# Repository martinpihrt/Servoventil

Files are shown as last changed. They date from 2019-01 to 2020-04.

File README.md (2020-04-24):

# Servoventil
Servoventil pro zalévací systém řízený procesorem ATTINY 1634 napájený z 5 AA baterií (celkem 6V). Zařízení je postavené z SMD součástek jako finální produkt za co nejméně peněz. Schéma zapojení obsahuje pouze nejnutněší součástky a procesor, který není zbytečně velký (rozměrově a programově). Deska obsahuje DIP spínač pro nastavení časů.  Programovací konektor ICSP 2x5 pinů, LED signalizující vybité baterie a chod zařízení, konektor pro připojení serva MG996R, startovací tlačítko, konektor pro sériovou linku (možnost komunikace s procesorem). Program pro procesor je napsán v prostředí Arduino IDE.  
Cena celého zařízení vychází bez serva na cca 225 Kč.

* Pohled na osazenou desku HW:1.0
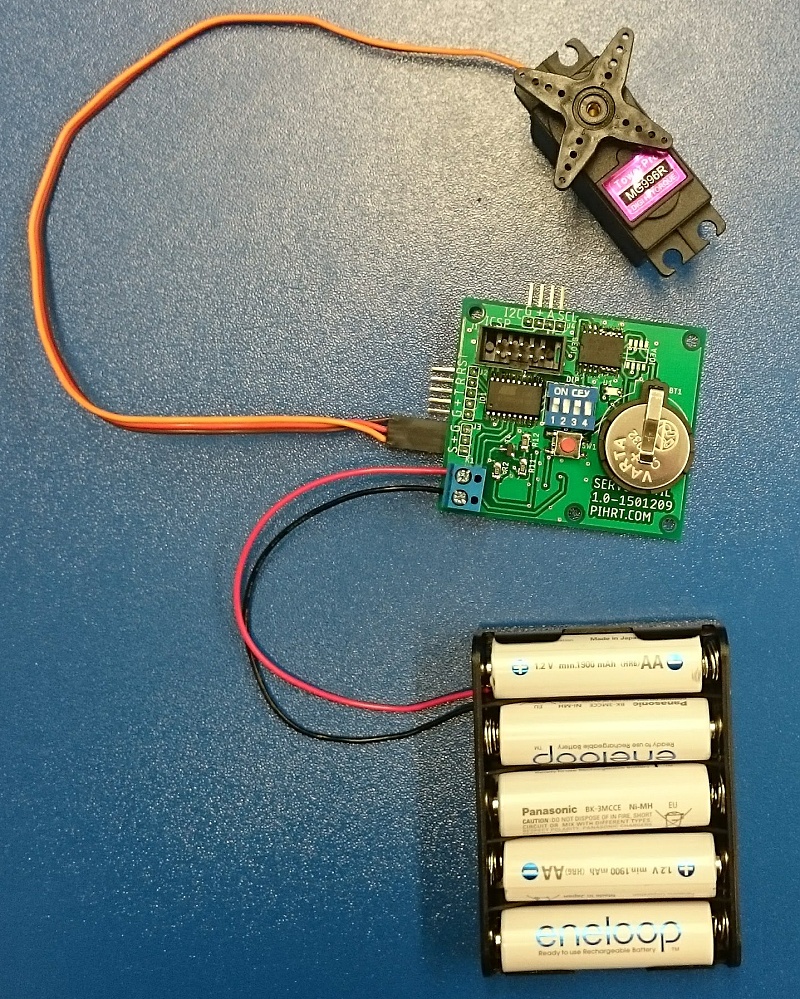
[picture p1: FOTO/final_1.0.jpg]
<br>
* Schéma zapojení HW:1.0
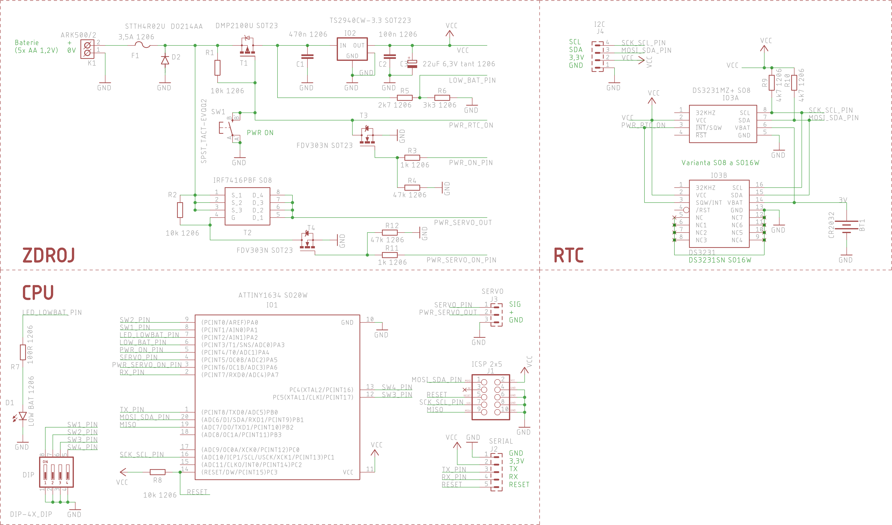
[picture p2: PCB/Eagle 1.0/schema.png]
<br>

# Funkce
## Uvedení do provozu
Po připojení napájení (5ks nabíjecí baterie AA 1,2V - celkem tedy 6-7V) čeká zařízení na stisk tlačítka. V tomto režimu neodebírá žádný proud z baterií (oba MOSFET tranzistory jsou udržovány uzavřené přes rezistory z kladného pólu). Časovač RTC ještě nebyl nastaven a má vloženu záložní baterii. Po stisknutí tlačítka na minimálně 1 sec se uzemní řídící vstup (gate) MOSFET tranzistoru, ten se otevře a přivede napájecí napětí na stabilizátor 3,3V. Za stabilizátorem je připojen procesor ATTINY 1634, který provede toto:
* sepne pomocný tranzistor, který podrží sepnutý (gate) u MOSFETu i po uvolnění tlačítka.
* změří napětí baterie (na AD vstupu procesoru je napětí z baterií 0-6V sníženo rezistorovým děličem na rozsah 0-3,3V). Napětí baterie se pohybuje (naprázdno) plně nabitého článku 1,4 V až napětí vybitého článku 1,0 V. Napětí pod 5V lze považovat za vybitý stav. Na AD vstupu naměříme hodnotu napětí (po zmenšení děličem) 2,6V. Pokud je baterie vybitá bliká LED dioda (3x blik, pauza, 3x blik...). RTC běží pouze z baterie a když je čas alarmu tak RTC přes svůj vnitřní tranzistor (otevřený kolektor) uzemní MOSFET, který sepne napájení pro stabilizátor a CPU. 
* přečte nastavené DIP spínače, sepne na určitý čas servo (napájení serva přes MOSFET a generuje signál pro odpovýdající směr a rychlost serva na určitou dobu) LED svítí -> ventil se otevře. Následně vypne napájení serva a čeká nastavenou dobu (dle DIP spínače 1-7 minut). Led bliká po dobu čekání otevření ventilu (krátké záblesky). Po nastavené době opět sepne napájení serva a ventil uzavře (LED svítí).
* nastaví čas (alarm) do RTC pro příští probuzení zařízení (cyklus 12, nebo 24 hodin).
* vypne veškeré napájení (běží pouze RTC z baterie).
* po nastavené době (DIP pozice 4: 12/24 hodin) RTC probudí CPU a opět se provede otevření ventilu na určitou dobu...

## DIP spínač má následující význam
Pozice 1-3 je BCD (dvojkový) kód pro nastvení doby otevření ventilu 1-7 minut.
* pozice 1 -> ON=1 minuta
* pozice 2 -> ON=2 minuty
* pozice 3 -> ON=4 minuty
Výsledný čas dle pozice 1-3 se sčítá. Příklad: čas otevření ventilu chceme 3 minuty -> DIP pozice 1 = ON, pozice 2 = ON, pozice 3 = OFF

Pozice 4 je čas probouzení.
* pozice 4 -> ON= 12 hodin, OFF= 24 hodin probouzení RTC časovače.

## Osazení desky spojů
Deska byla vyrobena u https://www.allpcb.com/.
* Pohled na desku TOP
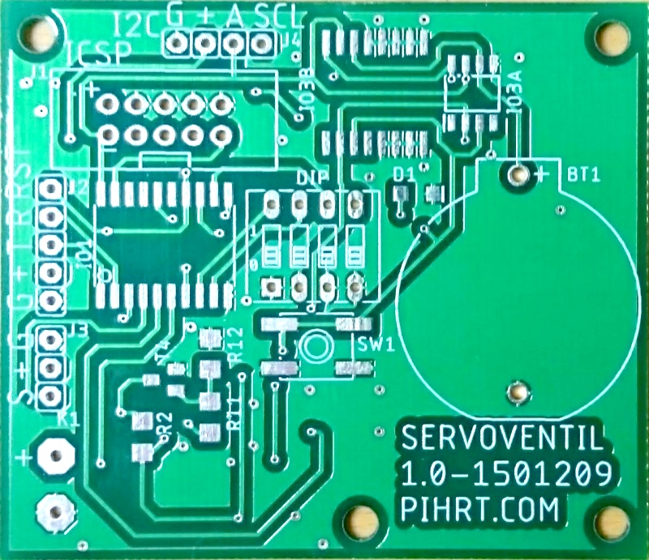
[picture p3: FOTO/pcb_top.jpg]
<br>
* Pohled na desku BOT
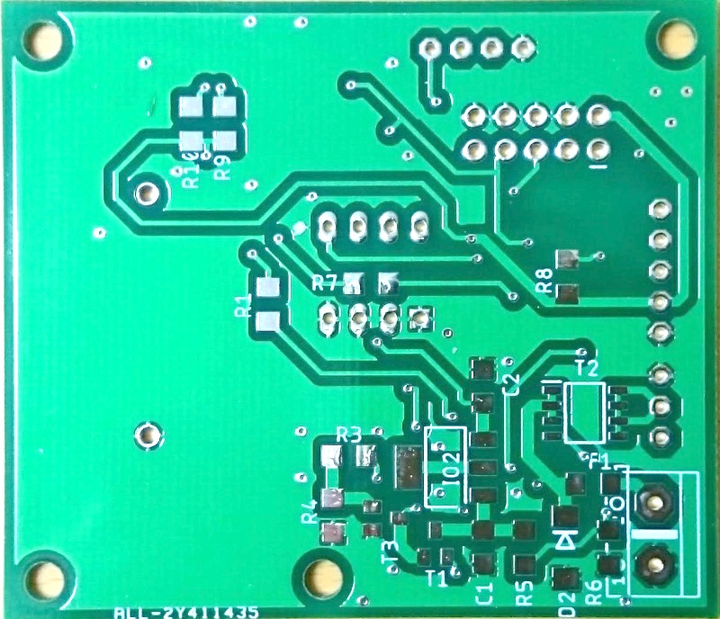
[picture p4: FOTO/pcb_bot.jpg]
<br>
První čím začneme je osazení SMD součástek z horní strany (TOP) a následně spodní (BOTTOM) strany. Po osazení SMD součástek zapájíme z horní strany THT (drátové) součástky - DIP spínače, držák baterie, napájecí konektor, řadové lišty. Před připojením napájení (baterie, nebo ICSP konektor) je potřeba desku pečlivě zkontrolovat na případné zkraty, nebo otočení součástek. Značení SMD rezistorů je následující: příklad text na rezistoru 1014 znamená 101 + 4 nuly tedy 101 0000 Ohmů, nebo 202 znamená 20 + 2 nuly tedy 20 00 Ohmů (2k).
Před připojením baterií (5ks AA) připojíme (pokud máme) napájecí zdroj s proudovou pojistkou, kterou nastavíme na 100 mA při 6V. Servo ani ICSP programátor není zatím k desce připojen. Obvod nemá v tuto chvíli ze zdroje odebírat žádný proud. Stiskneme a držíme tlačítko SW1 zmačknuté. Multimetrem (voltmetrem) změříme napětí na procesoru, RTC nebo stabilizátoru 3,3V. Napětí musí být cca 3,3V (při 6V na zdroji). Proud ze zdroje bude stále nepatrný (pár mA) - pouze se napájí procesor. Pokud se neobjevil problém (zkrat, velký podezřelý odběr proudu ze zdroje atd...) můžeme odpojit zdroj a zkusit připojit ICSP programátor. Nastavíme Arduino IDE na správný procesor a ICSP programátor. V tuto chvíli by již měl jít do procesoru nahrávat kód. Pokud připojíme na UART (sériovou linku) převodník, můžeme sledovat ladící výpisy co se aktuálně v procesoru odehrává. Protože je RTC obvod DS3231 jako samostatná součástka velmi drahý (okolo 200,-), tak ho odpájíme z China desky (ta se dá pořídit za 30,-).
* Pohled na osazenou desku TOP
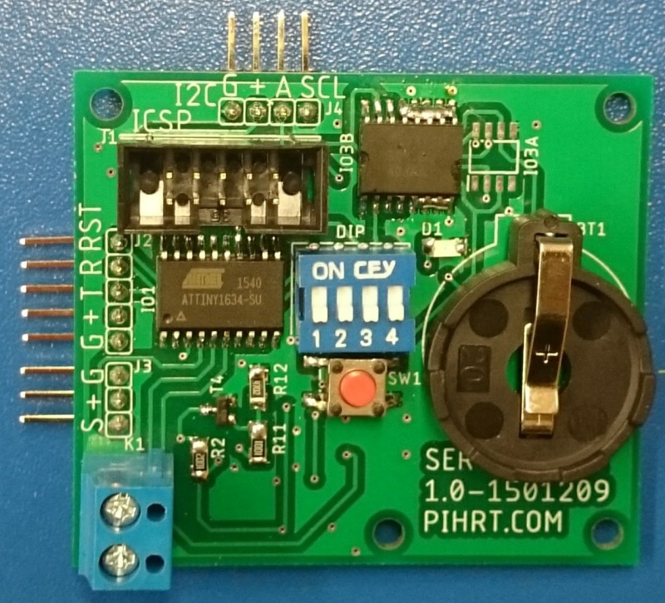
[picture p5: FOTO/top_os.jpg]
<br>
* Pohled na osazenou desku BOT
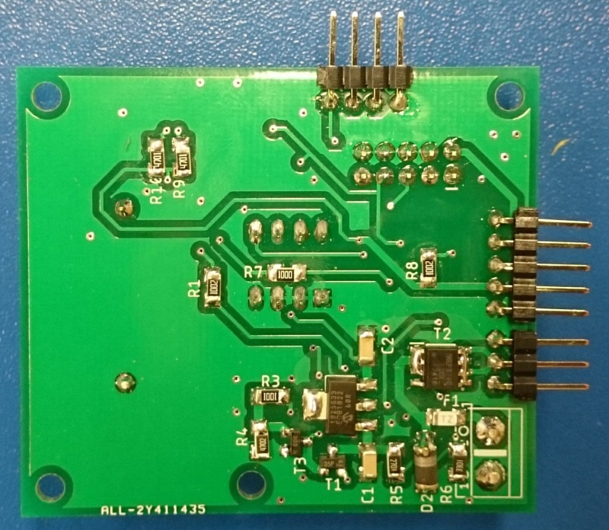
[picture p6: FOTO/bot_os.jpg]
<br>
* Připojení ICSP programátoru a USB-UART převodníku
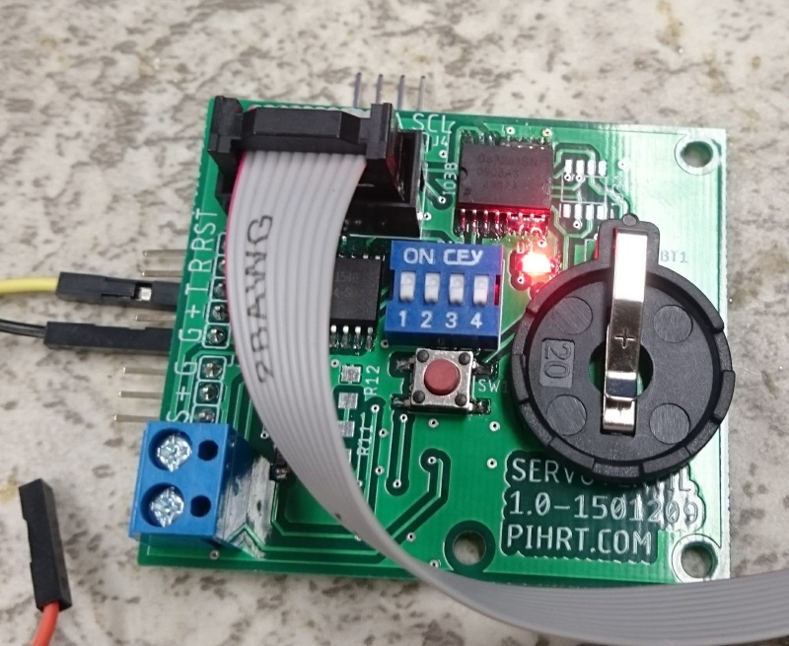
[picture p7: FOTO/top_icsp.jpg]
<br>
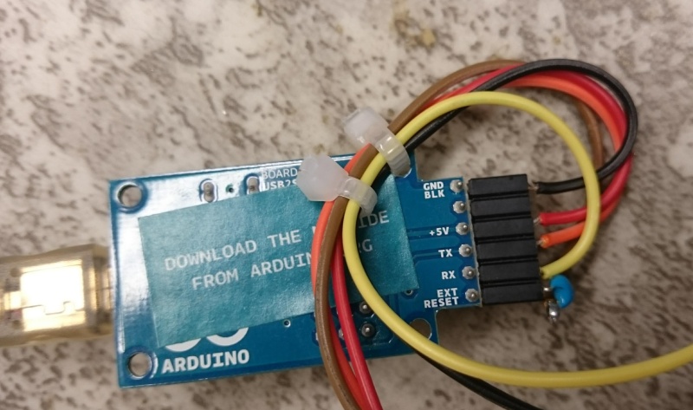
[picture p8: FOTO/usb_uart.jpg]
<br>
* Deska RTC s DS3231 (před vypájením a po vypájení)
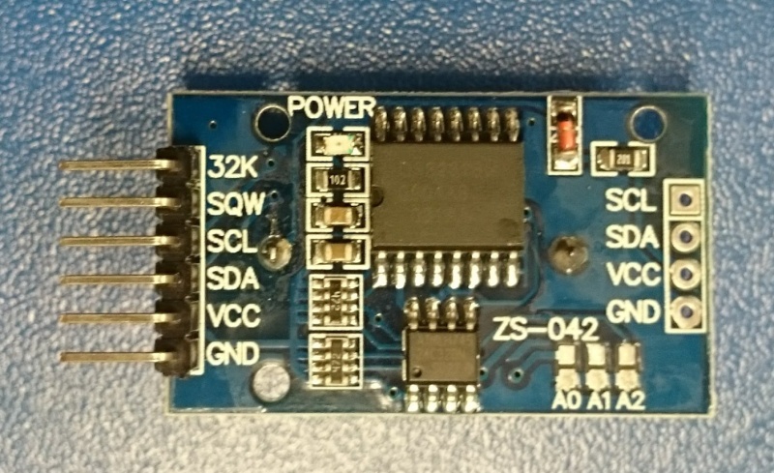
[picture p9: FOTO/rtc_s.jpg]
<br>
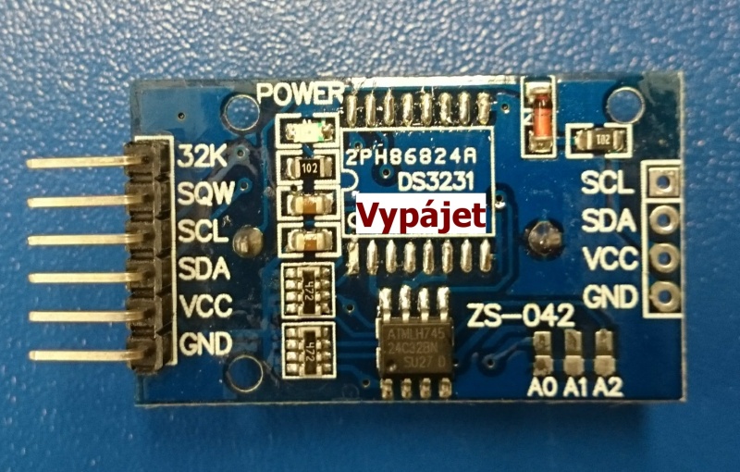
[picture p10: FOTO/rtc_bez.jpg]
<br>

## Přidání podpory pro procesor ATTINY 1634 do Arduino IDE
Spustíme nainstalované Arduino v našem počítači a otevřeme záložku "Soubor -> vlastnosti" a do správce dalších desek URL přidáme tento odkaz
http://drazzy.com/package_drazzy.com_index.json ze stránek [GitHub drazzy](https://github.com/SpenceKonde/ATTinyCore/blob/master/Installation.md). Následně potvrdíme tlačítkem "OK". Otevřeme v Arduinu záložku "Nástroje -> Vývojová deska -> Manažér desek" v otevřeném seznamu si vybereme "ATTinyCore by Spencle Konde" a přidáme do Arduina tlačítkem "instalace". V nastavení Arduino IDE je po těchto krocích možné využívat i jiné procesory než které jsou ve výchozí instalaci Arduina.

## Nahrání programu do desky - ICSP programátor
Připojíme do konektoru ICSP desky servoventilu náš programátor (pokud ho nemáme zakoupený, můžeme si ho vyrobit dle [tohoto návodu](https://pihrt.com/elektronika/390-programator-atmel-isp-usbasp)). Při připojení programátoru nepoužíváme napájení z baterií (baterie odpojíme)!

# Verze FW
* 1.0.0 výchozí verze programu 
* 0.0.0 výchozí verze programu - test všech periferií

# Verze HW
* 1.0 15.1.2019 výchozí verze desky 

# Licence
Creative Commons Attribution Share Alike 4.0
cc-by-sa-4.0

Na projektu se podílejí:
HW a FW Martin Pihrt - www.pihrt.com

# Aktuálně, TODO
## 23.4.2020
* Pracuji na verzi FW 1.0.0 (funkce dle popisu DIP a uvedení do provozu)

## 18.2.2019
* HW je otestován a plně funkční: pro test použit FW:0.0.0. Článek NiMh má 1,2 V. Napětí (naprázdno) plně nabitého článku je 1,4 V. Napětí vybitého článku je 1,0 V. Máme 5 článků -> napětí se bude pohybovat od 5V do 7V. Pod 5V je vybito LED blikne 2x krátce. Běží program - LED bliká rychle.

Výpis ze seriové linky (2 minuty probouzení)  
FW:0.0.0,18.2.2019,11:13:33  
RTC init...OK  
DIP1-4 init...OK  
DIP1=0 DIP2=1 DIP3=0 DIP4=1  
Baterie=5.86V  
Servo init...OK  
RTC nastavuji interval...OK  
Baterie=5.78V  
Baterie=5.85V  
Vypinam!

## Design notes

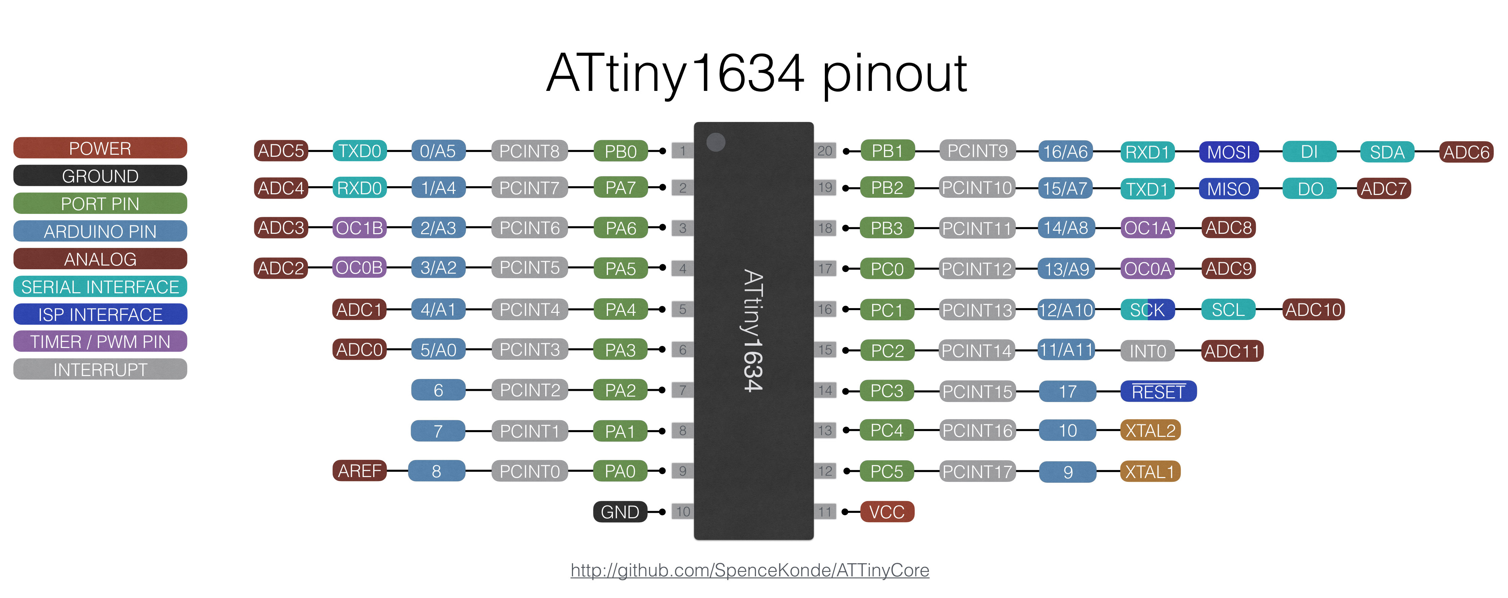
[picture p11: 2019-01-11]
FW/pinout attiny1634.jpg

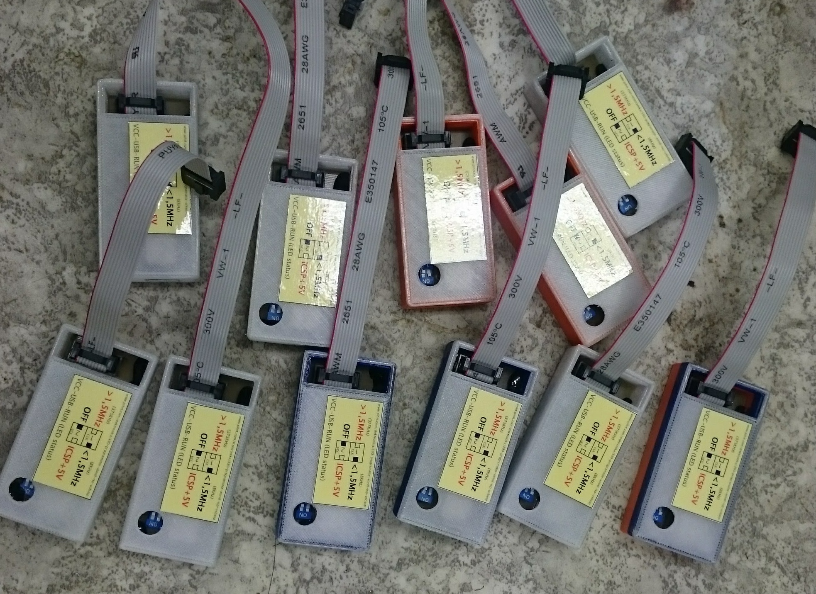
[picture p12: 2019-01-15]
FOTO/icsp_2.jpg

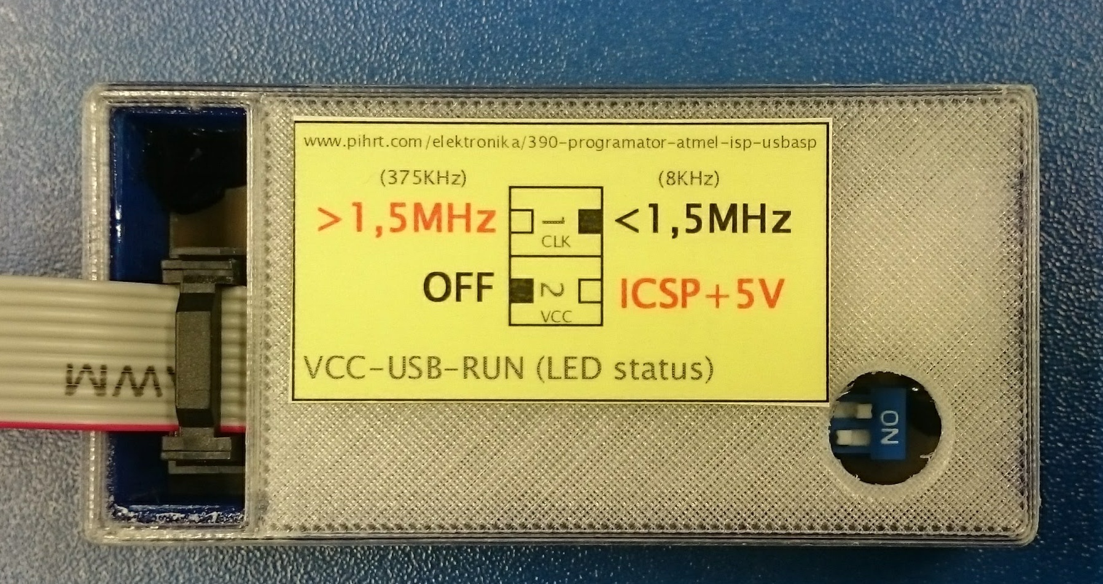
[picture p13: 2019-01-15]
FOTO/icsp_1.jpg

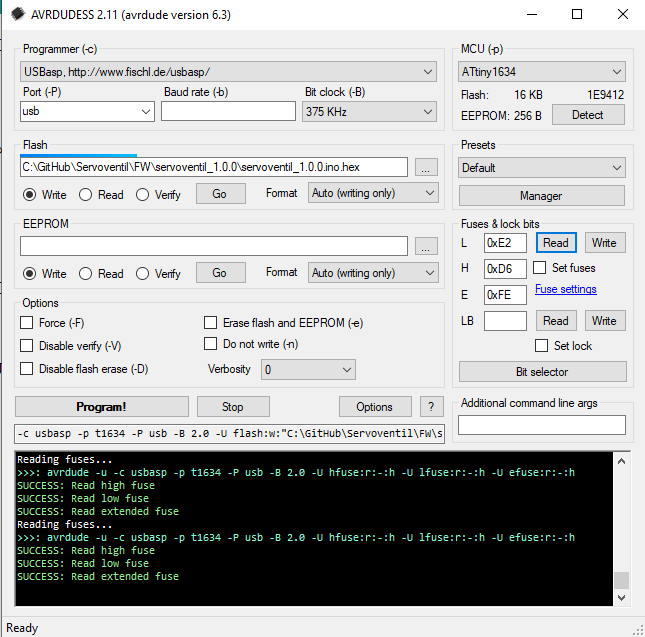
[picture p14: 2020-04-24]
FOTO/avrdudess.png

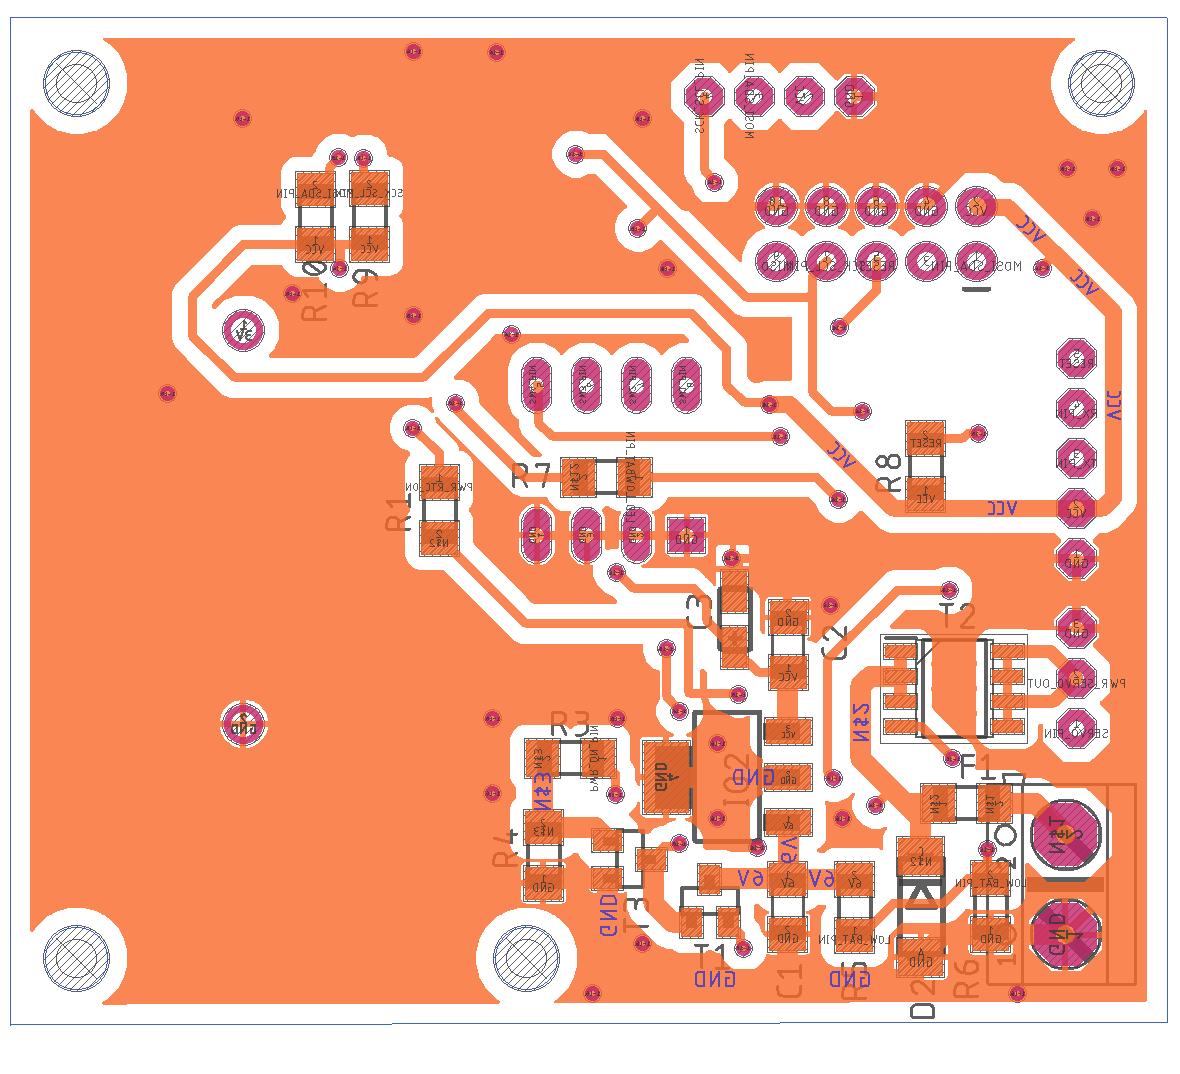
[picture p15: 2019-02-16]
PCB/Eagle 1.0/bot.png

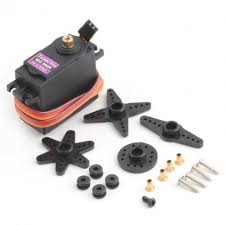
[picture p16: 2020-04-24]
DATASHEET/servo.jpg

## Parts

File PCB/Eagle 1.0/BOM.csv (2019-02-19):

Part | Value | Device | Package | Description
BT1 | CR2032 | BATTERY-20MM_PTH | BATTCOM_20MM_PTH | Battery - Single Cell
C1 | 470n 1206 | C-EUC1206 | C1206 | CAPACITOR, European symbol
C2 | 100n 1206 | C-EUC1206 | C1206 | CAPACITOR, European symbol
C3 | 22uF 6,3V tant 1206 | CPOL-EUCT3216 | CT3216 | POLARIZED CAPACITOR, European symbol
D1 | LOW BAT 1206 | LED1206 | LED-1206 | LED (Generic)
D2 | STTH4R02U DO214AA | DIODE-DO214AA | DO214AA | DIODE
DIP | DIP-4X_DIP | DIP-4X_DIP | DIP-4X | DIP Prepinac - 4x
F1 | 3,5A 1206 | PTCFUSE-1206 | R1206 | PTC fuses, resettable thermistors
IO1 | ATTINY1634 SO20W | ATTINY1634-SU | SOIC20 | ATtiny1634
IO2 | TS2940CW-3.3 SOT223 | MCP1825_SOT223 | SOT-223-3 | Microchip MCP1824 LDO Voltage Regulator
IO3A | DS3231MZ+ SO8 | DS3231MZ+ | SOIC127P600X175-8N | Real Time Clock 5+/-ppm RTC
IO3B | DS3231SN SO16W | DS3231/SO | SO16W
J1 | ICSP 2x5 | AVR_SPI_PROG_5X2LOCK | 2X5-SHROUDED_LOCK | AVR 10-pin ICSP Header
J2 | SERIAL | S1G5_JUMP | S1G5_JUM | Radove konektory - koliky - 5x
J3 | SERVO | S1G3_JUMP | S1G3_JUM | Radove konektory - koliky - 3x
J4 | I2C | S1G4_JUMP | S1G4_JUM | Radove konektory - koliky - 4x
K1 | ARK500/2 | ARK500/2 | ARK500/2 | Svorkovnice - roztec 5mm - dvojita
R1 | 10k 1206 | R-EU_R1206 | R1206 | RESISTOR, European symbol
R2 | 10k 1206 | R-EU_R1206 | R1206 | RESISTOR, European symbol
R3 | 1k 1206 | R-EU_R1206 | R1206 | RESISTOR, European symbol
R4 | 47k 1206 | R-EU_R1206 | R1206 | RESISTOR, European symbol
R5 | 2k7 1206 | R-EU_R1206 | R1206 | RESISTOR, European symbol
R6 | 3k3 1206 | R-EU_R1206 | R1206 | RESISTOR, European symbol
R7 | 100R 1206 | R-EU_R1206 | R1206 | RESISTOR, European symbol
R8 | 10k 1206 | R-EU_R1206 | R1206 | RESISTOR, European symbol
R9 | 4k7 1206 | R-EU_R1206 | R1206 | RESISTOR, European symbol
R10 | 4k7 1206 | R-EU_R1206 | R1206 | RESISTOR, European symbol
R11 | 1k 1206 | R-EU_R1206 | R1206 | RESISTOR, European symbol
R12 | 47k 1206 | R-EU_R1206 | R1206 | RESISTOR, European symbol
SW1 | SPST_TACT-EVQQ2 | SPST_TACT-EVQQ2 | EVQ-Q2 | SMT 6mm switch, EVQQ2 series
T1 | DMP2100U SOT23 | MOSFET-P-SOT23 | SOT-23 | P-Channel MOSFET with integrated body diode
T2 | IRF7416PBF SO8 | IRF7416PBF | SOIC127P600X175-8N | MOSFET P-Channel 30V 10A HEXFET SOIC8 Infineon IRF7416PBF P-channel MOSFET Transistor, 10 A, 30 V, 8-Pin SOIC
T3 | FDV303N SOT23 | MOSFET-N-SOT23 | SOT-23 | N-Channel MOSFET
T4 | FDV303N SOT23 | MOSFET-N-SOT23 | SOT-23 | N-Channel MOSFET

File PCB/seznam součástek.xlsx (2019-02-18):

Položka | Hodnota | Pouzdro | Odkaz e-shop | Cena ks | Počet ks | Celkem za ks
BT1A | CR2032 baterie | CR2032 | https://www.tme.eu/cz/details/bat-cr2032_va/baterie/varta-microbattery/6032-101-501/ | 7.0 Kč | 1 | 7.0 Kč
BT1B | CR2032 držák | CR2032 | https://www.tme.eu/cz/details/ch25-2032/baterie-pouzdra-i-drzaky/comf/ch25-2032lf/ | 8.0 Kč | 1 | 8.0 Kč
C1 | 470n 1206 | C1206 | https://www.tme.eu/cz/details/12065c474k4t2a/kondenzatory-mlcc-smd-1206/avx/ | 1.7 Kč | 1 | 1.7 Kč
C2 | 100n 1206 | C1206 | https://www.tme.eu/cz/details/12065c104kat2a/kondenzatory-mlcc-smd-1206/avx/ | 2.0 Kč | 1 | 2.0 Kč
C3 | 22uF 6,3V tant 1206 | CT3216 | https://www.tme.eu/cz/details/taja226k006r/tantalove-kondenzatory-smd/avx/taja226k006rnj/ | 5.4 Kč | 1 | 5.4 Kč
D1 | LOW BAT 1206 | LED-1206 | https://www.tme.eu/cz/details/osr51206c1e/diody-led-smd-barevne/optosupply/ | 1.0 Kč | 1 | 1.0 Kč
D2 | STTH4R02U | DO214AA | https://www.tme.eu/cz/details/stth4r02u/univerzalni-diody-smd/st-microelectronics/ | 6.0 Kč | 1 | 6.0 Kč
DIP | DIP-4X_DIP | DIP-4X | https://www.tme.eu/cz/details/ds-04/prepinace-dip-switch/ninigi/ | 19.0 Kč | 1 | 19.0 Kč
F1 | 3,5A 1206 | R1206 | https://www.tme.eu/cz/details/c1t-3.5/pojistky-smd-1206-zpozdene/bel-fuse/0685t3500-01/ | 6.0 Kč | 1 | 6.0 Kč
IO1 | ATTINY1634 SO20W | SOIC20 | https://www.tme.eu/cz/details/attiny1634-su/rodina-avr-8-bitu/microchip-atmel/ | 34.0 Kč | 1 | 34.0 Kč
IO2 | TS2940CW-3.3 SOT223 | SOT-223-3 | https://www.tme.eu/cz/details/ts2940cw-3.3/stabilizatory-napeti-neregulovane-ldo/taiwan-semiconductor/ | 17.0 Kč | 1 | 17.0 Kč
IO3A | DS3231MZ+ SO8 | SOIC127P600X175-8N | alternativa místo SO16W | 0.0 Kč | 1 | 0.0 Kč
IO3B | DS3231SN SO16W | SO16W | https://www.tme.eu/cz/details/oky3393/moduly-rtc/okystar/ | 50.0 Kč | 1 | 50.0 Kč
J1 | ICSP 2x5 | 2X5-SHROUDED_LOCK | https://www.tme.eu/cz/details/zl231-10pg/konektory-idc/connfly/ds1013-10ssib1/ | 2.2 Kč | 1 | 2.2 Kč
J2 | SERIAL | S1G5_JUM | https://www.tme.eu/cz/details/zl201-05g/konektory-hrebinky/connfly/ds1021-1_5sf1-1/ | 0.8 Kč | 1 | 0.8 Kč
J3 | SERVO | S1G3_JUM | https://www.tme.eu/cz/details/zl201-03g/konektory-hrebinky/connfly/ds1021-1_3sf1-1/ | 0.5 Kč | 1 | 0.5 Kč
J4 | I2C | S1G4_JUM | https://www.tme.eu/cz/details/zl201-04g/konektory-hrebinky/connfly/ds1021-1_4sf1-1/ | 0.9 Kč | 1 | 0.9 Kč
K1 | ARK500/2 | ARK500/2 | https://www.tme.eu/cz/details/ebba-02-c-ss-bu/svorkovnice-do-plosnych-spoju/adam-tech/ | 3.3 Kč | 1 | 3.3 Kč
R1, R2, R8 | 10k 1206 | R1206 | https://www.tme.eu/cz/details/crcw120610k0fktabc/rezistory-smd-1206/vishay/ | 0.7 Kč | 3 | 2.1 Kč
R3, R11 | 1k 1206 | R1206 | https://www.tme.eu/cz/details/cq1206-1k-1%25/rezistory-smd-1206/royal-ohm/cq06s4f1001t5e/ | 0.5 Kč | 2 | 1.0 Kč
R4, R12 | 47k 1206 | R1206 | https://www.tme.eu/cz/details/cq1206-47k-1%25/rezistory-smd-1206/royal-ohm/cq06s4f4702t5e/ | 0.5 Kč | 2 | 1.0 Kč
R5 | 2k7 1206 | R1206 | https://www.tme.eu/cz/details/smd1206-2k7-1%25/rezistory-smd-1206/royal-ohm/1206s4f2701t5e/ | 0.6 Kč | 1 | 0.6 Kč
R6 | 3k3 1206 | R1206 | https://www.tme.eu/cz/details/smd1206-3k3-1%25/rezistory-smd-1206/royal-ohm/1206s4f3301t5e/ | 0.6 Kč | 1 | 0.6 Kč
R7 | 100R 1206 | R1206 | https://www.tme.eu/cz/details/smd1206-100r/rezistory-smd-1206/royal-ohm/1206s4j0101t5e/ | 0.3 Kč | 1 | 0.3 Kč
R9, R10 | 4k7 1206 | R1206 | https://www.tme.eu/cz/details/cq1206-4k7-1%25/rezistory-smd-1206/royal-ohm/cq06s4f4701t5e/ | 0.5 Kč | 2 | 1.0 Kč
SW1 | SPST_TACT-EVQQ2 | EVQ-Q2 | https://www.tme.eu/cz/details/tactm-69n-f/mikrospinace-tact/ninigi/ | 1.5 Kč | 1 | 1.5 Kč
T1 | DMP2100U SOT23 | SOT-23 | https://www.tme.eu/cz/details/dmp2100u-7/tranzistory-s-kanalem-p-smd/diodes-incorporated/ | 2.0 Kč | 1 | 2.0 Kč
T2 | IRF7416PBF SO8 | SOIC127P600X175-8N | https://www.tme.eu/cz/details/irf7416pbf/tranzistory-s-kanalem-p-smd/infineon-irf/ | 13.0 Kč | 1 | 13.0 Kč
T3, T4 | FDV303N SOT23 | SOT-23 | https://www.tme.eu/cz/details/fdv303n/tranzistory-s-kanalem-n-smd/on-semiconductor/ | 2.0 Kč | 2 | 4.0 Kč
PCB | Plošný spoj | 51mm * 59mm , 2 vrstvy | https://www.allpcb.com/ (10ks za $14.43) (https://www.allpcb.com/%20(10ks%20za%20$14.43)) | 33.0 Kč | 1 | 33.0 Kč
Celkem |  |  |  |  |  | 224.9 Kč

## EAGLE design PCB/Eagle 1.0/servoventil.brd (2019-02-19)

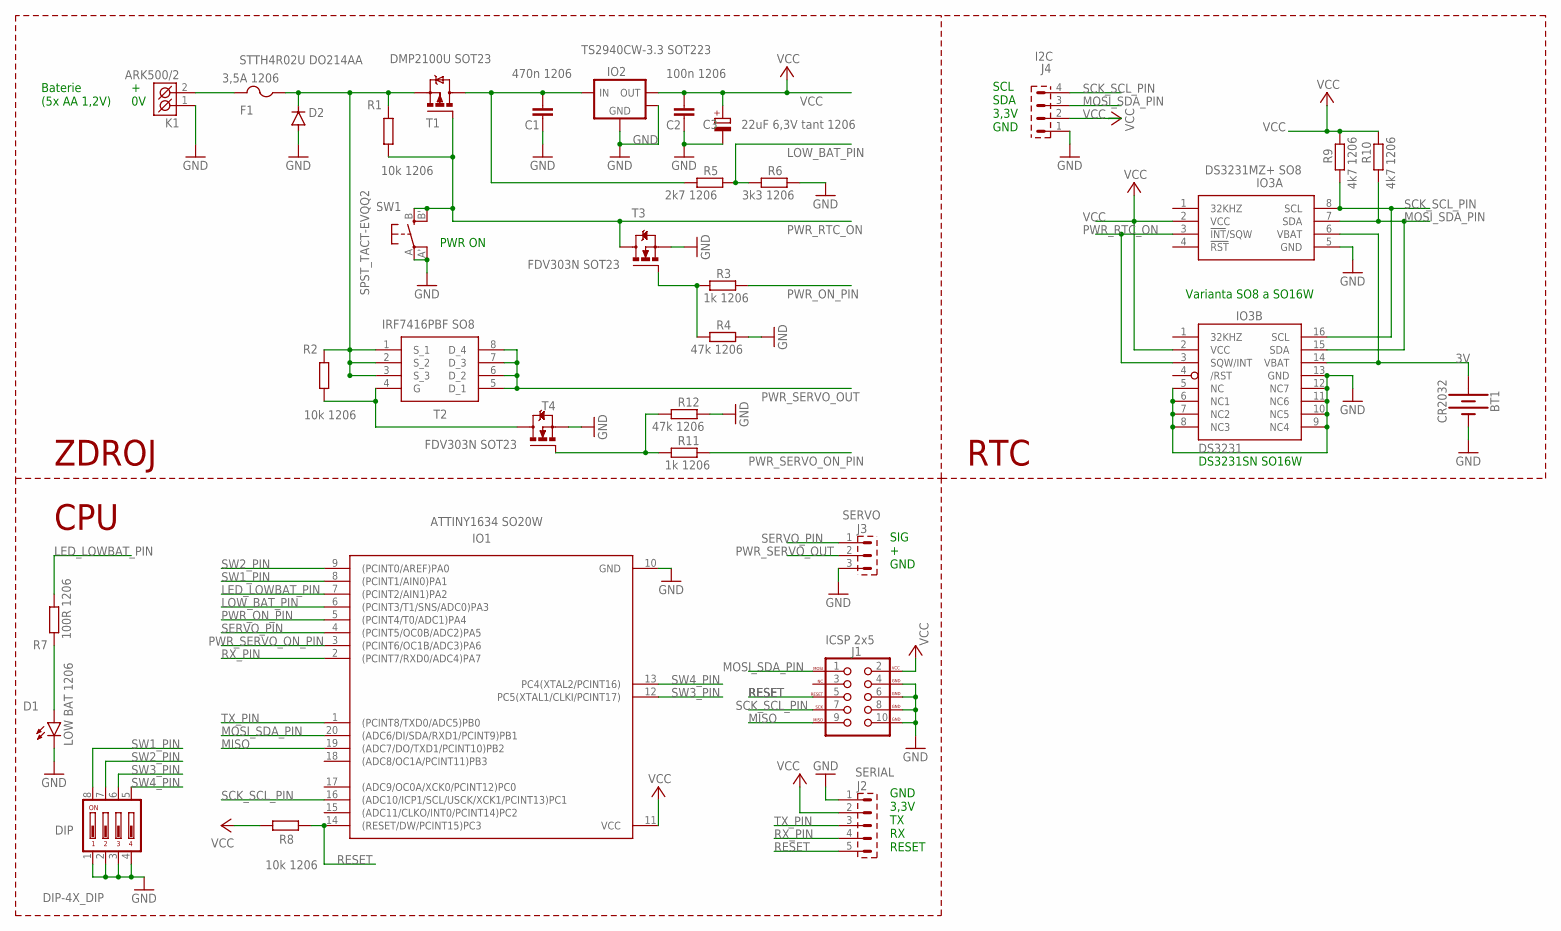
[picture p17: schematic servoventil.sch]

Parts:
BT1: CR2032; BATTCOM_20MM_PTH
C1: 470n 1206; C1206
C2: 100n 1206; C1206
C3: 22uF 6,3V tant 1206; CT3216
D1: LOW BAT 1206; LED-1206
D2: STTH4R02U DO214AA; DO214AA
DIP: DIP-4X_DIP; DIP-4X
F1: 3,5A 1206; R1206
IO1: ATTINY1634 SO20W; SOIC20
IO2: TS2940CW-3.3 SOT223; SOT-223-3
IO3A: DS3231MZ+ SO8; SOIC127P600X175-8N
IO3B: DS3231SN SO16W; SO16W
J1: ICSP 2x5; 2X5-SHROUDED_LOCK
J2: SERIAL; S1G5_JUM
J3: SERVO; S1G3_JUM
J4: I2C; S1G4_JUM
K1: ARK500/2
R1, R2, R8: 10k 1206; R1206
R3, R11: 1k 1206; R1206
R4, R12: 47k 1206; R1206
R5: 2k7 1206; R1206
R6: 3k3 1206; R1206
R7: 100R 1206; R1206
R9, R10: 4k7 1206; R1206
SW1: SPST_TACT-EVQQ2; EVQ-Q2
T1: DMP2100U SOT23; SOT-23
T2: IRF7416PBF SO8; SOIC127P600X175-8N
T3, T4: FDV303N SOT23; SOT-23

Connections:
3V: BT1.1 (+), IO3A.6 (VBAT), IO3B.14 (VBAT)
6V: C1.1, IO2.1 (VIN), R5.2, T1.3 (D)
GND: BT1.2 (-), C1.2, C2.2, C3.-, D1.C, D2.A, DIP.1, DIP.2, DIP.3, DIP.4, IO1.10 (GND), IO2.2 (GND), IO2.4 (HEATSINK), IO3A.5 (GND), IO3B.5 (NC), IO3B.6 (NC1), IO3B.7 (NC2), IO3B.8 (NC3), IO3B.9 (NC4), IO3B.10 (NC5), IO3B.11 (NC6), IO3B.12 (NC7), IO3B.13 (GND), J1.4 (GND), J1.6 (GND), J1.8 (GND), J1.10 (GND), J2.1, J3.3, J4.1, K1.1 (K1), R4.1, R6.1, R12.1, SW1.A, SW1.A' (P1), T3.2 (S), T4.2 (S)
LED_LOWBAT_PIN: IO1.7 ((PCINT2/AIN1)PA2), R7.1
LOW_BAT_PIN: IO1.6 ((PCINT3/T1/SNS/ADC0)PA3), R5.1, R6.2
MISO: IO1.19 ((ADC7/DO/TXD1/PCINT10)PB2), J1.9 (MISO)
MOSI_SDA_PIN: IO1.20 ((ADC6/DI/SDA/RXD1/PCINT9)PB1), IO3A.7 (SDA), IO3B.15 (SDA), J1.1 (MOSI), J4.3, R10.2
unnamed: F1.2, K1.2 (K2)
unnamed: D2.C, F1.1, R1.2, R2.2, T1.2 (S), T2.1 (S_1), T2.2 (S_2), T2.3 (S_3)
unnamed: R3.2, R4.2, T3.1 (G)
unnamed: R2.1, T2.4 (G), T4.3 (D)
unnamed: R11.2, R12.2, T4.1 (G)
unnamed: D1.A, R7.2
PWR_ON_PIN: IO1.5 ((PCINT4/T0/ADC1)PA4), R3.1
PWR_RTC_ON: IO3A.3 (!INT!/SQW), IO3B.3 (SQW/INT), R1.1, SW1.B (S), SW1.B' (S1), T1.1 (G), T3.3 (D)
PWR_SERVO_ON_PIN: IO1.3 ((PCINT6/OC1B/ADC3)PA6), R11.1
PWR_SERVO_OUT: J3.2, T2.5 (D_1), T2.6 (D_2), T2.7 (D_3), T2.8 (D_4)
RESET: IO1.14 ((RESET/DW/PCINT15)PC3), J1.5 (RESET), J2.5, R8.2
RX_PIN: IO1.2 ((PCINT7/RXD0/ADC4)PA7), J2.4
SCK_SCL_PIN: IO1.16 ((ADC10/ICP1/SCL/USCK/XCK1/PCINT13)PC1), IO3A.8 (SCL), IO3B.16 (SCL), J1.7 (SCK), J4.4, R9.2
SERVO_PIN: IO1.4 ((PCINT5/OC0B/ADC2)PA5), J3.1
SW1_PIN: DIP.8, IO1.8 ((PCINT1/AIN0)PA1)
SW2_PIN: DIP.7, IO1.9 ((PCINT0/AREF)PA0)
SW3_PIN: DIP.6, IO1.12 (PC5(XTAL1/CLKI/PCINT17))
SW4_PIN: DIP.5, IO1.13 (PC4(XTAL2/PCINT16))
TX_PIN: IO1.1 ((PCINT8/TXD0/ADC5)PB0), J2.3
VCC: C2.1, C3.+, IO1.11 (VCC), IO2.3 (VOUT), IO3A.2 (VCC), IO3B.2 (VCC), J1.2 (VCC), J2.2, J4.2, R8.1, R9.1, R10.1

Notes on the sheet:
+ 0V
Baterie (5x AA 1,2V)
ZDROJ
CPU
RTC
GND 3,3V TX RX RESET
PWR ON
Varianta SO8 a SO16W
DS3231SN SO16W
SIG + GND
SCL SDA 3,3V GND

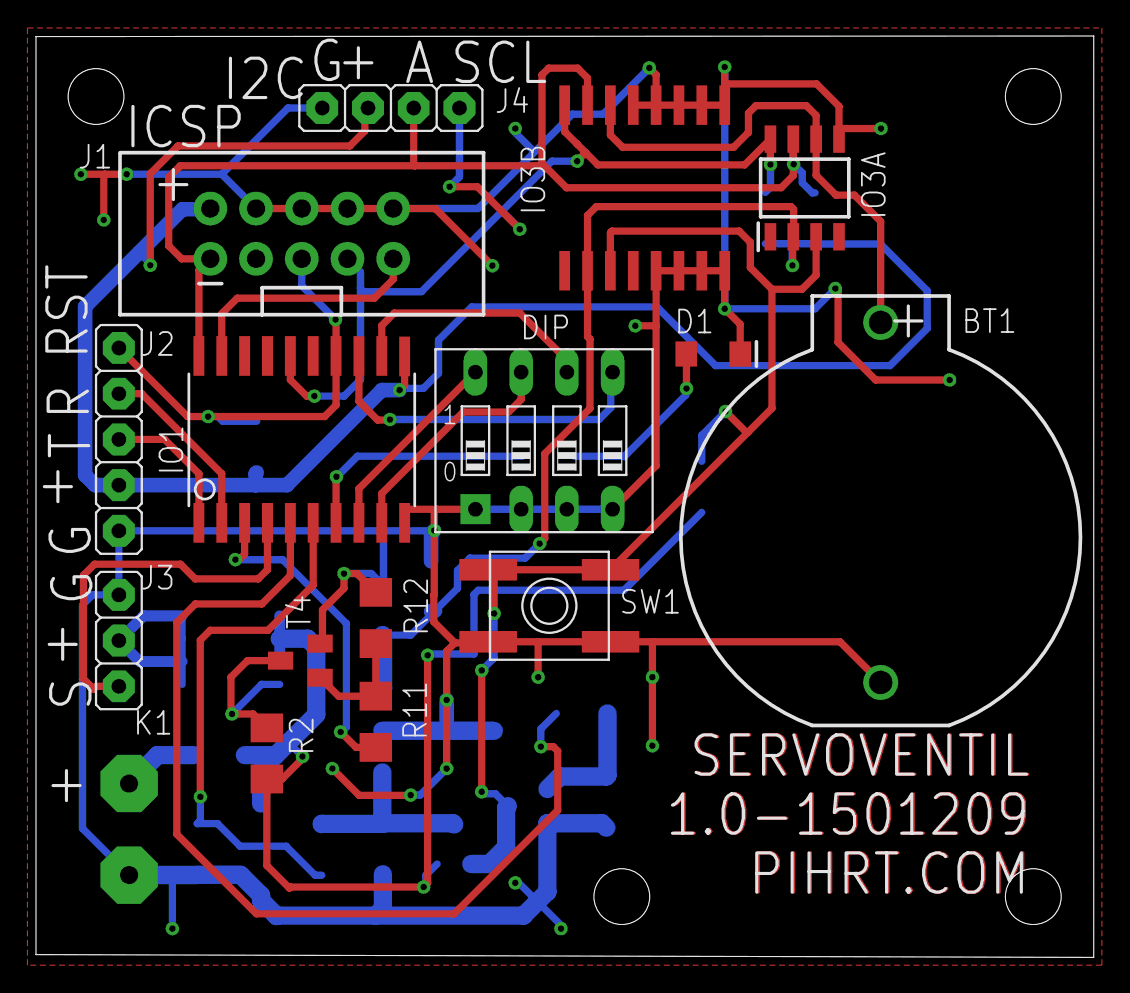
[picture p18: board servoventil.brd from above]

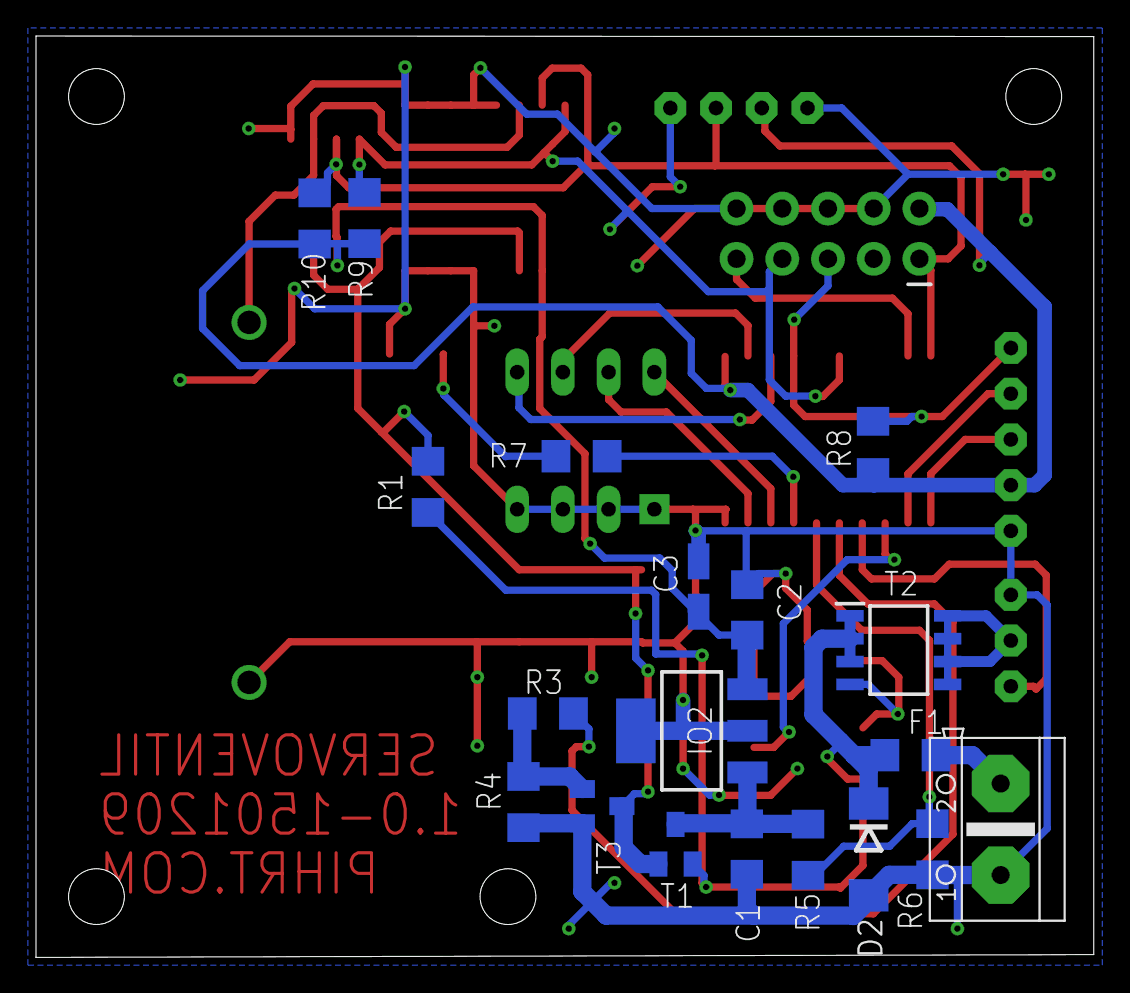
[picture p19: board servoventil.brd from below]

Board: 2 copper layers, 58.8 x 51.2 mm, 34 parts (19 on the bottom side), 27 nets.

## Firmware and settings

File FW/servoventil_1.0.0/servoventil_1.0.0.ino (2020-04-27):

// záložka cti_me!
#define FW    "1.0.0"  // aktuální verze FW 27.4.2020

// přiřazení pinů na procesoru ATTINY 1634
//#define SCK_SCL_PIN            12   // PC1 pin 16 pro info  (SCK je na stejném vodiči jako SCL)
//#define MOSI_SDA_PIN           16   // PB1 pin 20 pro info  (MOSI je na stejném vodiči jako SDA)
//#define RX_PIN                 1    // PA7 pin 2  pro info
//#define TX_PIN                 0    // PB0 pin 1  pro info
#define PWR_SERVO_ON_PIN         2    // PA6 pin 3  spíná napájení serva
#define SERVO_PIN                3    // PA5 pin 4  výstup pro servo PWM
#define PWR_ON_PIN               4    // PA4 pin 5  spíná samodržení napájení procesoru
#define LOW_BAT_PIN              A0   // PA3 pin 6  jako A0 vstup z baterie, že je málé napájení baterie
#define LED_LOWBAT_PIN           6    // PA2 pin 7  výstup pro LED, že je málé napájení baterie
#define SW1_PIN                  7    // PA1 pin 8  vstup DIP přepínač 1
#define SW2_PIN                  8    // PA0 pin 9  vstup DIP přepínač 2
#define SW3_PIN                  9    // PC5 pin 12 vstup DIP přepínač 3
#define SW4_PIN                  10   // PC4 pin 13 vstup DIP přepínač 4

#define VENTIL_OTEVRENO_UHEL     89   // úhel serva pro otevření vody
#define VENTIL_ZAVRENO_UHEL      3    // úhel serva pro zavření vody
#define DOBA_PREBEHU_SERVA    2000    // 2000 ms -> 2 sec (8MHz) (nesmí být delší než 4 sec, jinak začne padat watchdog!)

#include <avr/wdt.h>                  // watchdog (hlídá chod CPU proti zamrznutí)

// UART
//#define USE_UART                      // pokud není zakomentované používat sériovou linku (pro zakázání zakomentuj//)
//#define BAUD   9600                   // rychlost sériové linky 9600, 19200, 38400, bd
//#define DEBUG                         // pokud není zakomentované používat na sériovou linku pomocné výpisy (pro zakázání zakomentuj//)

// SERVO
#define USE_SERVO                     // pokud není zakomentované používat servo
  
// DS3231 (RTC na adrese 0x68)
#define USE_WIRE                      // používat I2C
#define USE_DS3231                    // pokud není zakomentované používat DS3231
#define DS_ADDRESS  0x68 
uint8_t SLEEP_PER = 2;                // nastavení intervalu spánku v minutách pro alarm v DS3231  

// Měření napájení pomocí A/D
//#define USE_AD                      // pokud není zakomentované používat měření napětí baterie pomocí AD
#define MIN_BATT    5.0               // minimální napětí z baterií
float volt;                           // napětí z baterií

// Časovač v loop
unsigned long previousMillis =    0;  // pomocná
const long interval =            100; // interval časovače

// Pomocné
bool hod_interval;                    // true = 24 hodin, false = 12 hodin interval probouzení (nastavuje DIP 4)
byte ZapNaDobu;                       // nastavení času otevření ventilu od 1 do 7 minut (nastavuje DIP 1-3)
byte pocet_hodin, pocet_minut;        // dle DIP se nastaví na 12:00 nebo 23:59 hodin interval pro RTC

//*******************************************************************
#ifdef DEBUG    
  #define DPRINT(...)    Serial.print(__VA_ARGS__)     
  #define DPRINTLN(...)  Serial.println(__VA_ARGS__)   
#else
  #define DPRINT(...)     
  #define DPRINTLN(...)   
#endif

#ifdef USE_SERVO 
  //https://github.com/platformio/platformio-pkg-framework-arduinoavr/tree/master/libraries/__cores__/tiny/Servo_ATTinyCore
  #include <Servo_ATTinyCore.h> // knihovna pro servo
  Servo servo;
#endif

#ifdef USE_WIRE
  #include "Wire.h"             // knihovna pro I2C
#endif

#ifdef USE_DS3231 
  #include "ds3231.h"          // knihovna pro DS3231
#endif

// makra pro datum kompilace
#define BUILDTM_YEAR (\
    __DATE__[7] == '?' ? 1900 \
    : (((__DATE__[7] - '0') * 1000 ) \
    + (__DATE__[8] - '0') * 100 \
    + (__DATE__[9] - '0') * 10 \
    + __DATE__[10] - '0'))

#define BUILDTM_MONTH (\
    __DATE__ [2] == '?' ? 1 \
    : __DATE__ [2] == 'n' ? (__DATE__ [1] == 'a' ? 1 : 6) \
    : __DATE__ [2] == 'b' ? 2 \
    : __DATE__ [2] == 'r' ? (__DATE__ [0] == 'M' ? 3 : 4) \
    : __DATE__ [2] == 'y' ? 5 \
    : __DATE__ [2] == 'l' ? 7 \
    : __DATE__ [2] == 'g' ? 8 \
    : __DATE__ [2] == 'p' ? 9 \
    : __DATE__ [2] == 't' ? 10 \
    : __DATE__ [2] == 'v' ? 11 \
    : 12)

#define BUILDTM_DAY (\
    __DATE__[4] == '?' ? 1 \
    : ((__DATE__[4] == ' ' ? 0 : \
    ((__DATE__[4] - '0') * 10)) + __DATE__[5] - '0'))

#define BUILDTIME __TIME__    

void getBATT(){
 #ifdef USE_AD 
   int in = analogRead(LOW_BAT_PIN);
   volt = (in * 6.0) / 1024.0; // při 6V je za děličem 3.3V tedy 1023 max Ubat
   #ifdef DEBUG
     DPRINT("Baterie");
     DPRINT("=");
     DPRINT(volt);
     DPRINTLN("V");
   #endif
 #endif
}//konec void    

void read_DIP(){
   ZapNaDobu = 0;                            // doba 1-7 minut dle DIP
   if(!digitalRead(SW1_PIN)) ZapNaDobu  = 1; // 1 minuta
   if(!digitalRead(SW2_PIN)) ZapNaDobu += 2; // 2 minuty
   if(!digitalRead(SW3_PIN)) ZapNaDobu += 4; // 4 minuty
   
   if(!digitalRead(SW4_PIN)) hod_interval = true;
   else                      hod_interval = false;

  if(hod_interval) { pocet_hodin = 23; pocet_minut = 59; } // 24 hodin interval
  else             { pocet_hodin = 12; pocet_minut = 0;  } // 12 hodin interval
  
  #ifdef DEBUG
     DPRINT("DIP 1-3: ");
     DPRINT(ZapNaDobu);
     DPRINT(" minut, DIP 4: ");
     if(hod_interval) DPRINTLN("24 hodin.");
     else             DPRINTLN("12 hodin.");
  #endif
}//konec void

byte decToBcd(byte val){
    return( (val/10*16) + (val%10) );
}//konec byte

void setDS3231time(byte second, byte minute, byte hour, byte dayOfWeek, byte dayOfMonth, byte month, byte year){
    // sets time and date data to DS3231
    // DS3231 seconds, minutes, hours, day, date, month, year
    // setDS3231time(30,42,21,4,26,11,14);
    Wire.beginTransmission(DS3231_I2C_ADDR); 
    Wire.write(0); // set next input to start at the seconds register
    Wire.write(decToBcd(second)); // set seconds
    Wire.write(decToBcd(minute)); // set minutes
    Wire.write(decToBcd(hour)); // set hours
    Wire.write(decToBcd(dayOfWeek)); // set day of week (1=Sunday, 7=Saturday)
    Wire.write(decToBcd(dayOfMonth)); // set date (1 to 31)
    Wire.write(decToBcd(month)); // set month
    Wire.write(decToBcd(year)); // set year (0 to 99)
    Wire.endTransmission();
}//konec void 

void set_next_alarm(void){
  #ifdef USE_DS3231 
    // nastavime datum a cas na 0:0:1 1.1.2020
    // DS3231 seconds, minutes, hours, day, date, month, year
    setDS3231time(1,0,0,1,1,1,20);

    // flags define what calendar component to be checked against the current time in order
    // to trigger the alarm
    // A2M2 (minutes) (0 to enable, 1 to disable)
    // A2M3 (hour)    (0 to enable, 1 to disable) 
    // A2M4 (day)     (0 to enable, 1 to disable)
    // DY/DT          (dayofweek == 1/dayofmonth == 0)
    byte flags[4] = { 0, 0, 1, 1 };
    // set Alarm2. only the minute is set since we ignore the hour and day component
    DS3231_set_a2(pocet_minut, pocet_hodin, 0, flags);
    // activate Alarm2
    DS3231_set_creg(DS3231_CONTROL_INTCN | DS3231_CONTROL_A2IE);
  #endif 
}//konec void 
  
//******************************************************************************************************************************

void setup() { // nastavení
  pinMode(PWR_ON_PIN,OUTPUT);         // pin pro samodržení napájení CPU
  pinMode(PWR_SERVO_ON_PIN,OUTPUT);   // pin pro napájení serva
  pinMode(SERVO_PIN,OUTPUT);          // pin pro PWM serva
  pinMode(LED_LOWBAT_PIN,OUTPUT);     // pin pro LED
  pinMode(LOW_BAT_PIN,INPUT);         // pin na AD
  pinMode(SW1_PIN,INPUT_PULLUP);      // pin DIP1 
  pinMode(SW2_PIN,INPUT_PULLUP);      // pin DIP2
  pinMode(SW3_PIN,INPUT_PULLUP);      // pin DIP3
  pinMode(SW4_PIN,INPUT_PULLUP);      // pin DIP4
  
  digitalWrite(PWR_ON_PIN,HIGH);      // podržet napájení (po uvolnění tlačítka)
  
  digitalWrite(PWR_SERVO_ON_PIN,LOW); // vypnout napájení serva
  digitalWrite(SERVO_PIN,LOW);        // vypnout výstup pro PWM serva      
  digitalWrite(LED_LOWBAT_PIN,HIGH);  // zapnout LED

  wdt_enable(WDTO_4S);                // povolit watchdog ping 4s
  wdt_reset();                        // vynulovat časovač pro wdt
  
  #ifdef USE_UART
     Serial.begin(BAUD);              // rychlost linky 
     delay(1000);                     // počkáme na UART
  #endif
  wdt_reset();                        // vynulovat časovač pro wdt
  
  #ifdef DEBUG
     DPRINTLN();
     DPRINT("FW:");
     DPRINT(FW);                      // verze FW
     DPRINT(",");
     DPRINT(BUILDTM_DAY);             // den
     DPRINT(".");
     DPRINT(BUILDTM_MONTH);           // měsíc
     DPRINT(".");
     DPRINT(BUILDTM_YEAR);            // rok
     DPRINT(",");
     DPRINTLN(BUILDTIME);             // čas kompilace  
  #endif  

  #ifdef USE_WIRE
     #ifdef DEBUG
       DPRINT("I2C init...");
     #endif 
     Wire.begin();                    // aktivace I2C 
  #endif
     
  #ifdef USE_DS3231 
    #ifdef DEBUG
       DPRINT("RTC init...");
    #endif                                     
    Wire.beginTransmission(DS_ADDRESS);           // probuď zařízení na 0x68
    if(Wire.endTransmission()==0) {               // test zda byla odpověď ze zařízení na adrese 0x68 (RTC DS3231)
       DS3231_init(DS3231_CONTROL_INTCN);         // aktivace DS3231
       DS3231_clear_a2f();                        // smazat příznak alarmu a nastavit pin INT na vysokou impedanci
       #ifdef DEBUG
          DPRINTLN("OK");
       #endif   
    }
    else {
      #ifdef DEBUG
         DPRINT("Chyba RTC na adrese: ");
         DPRINTLN(DS_ADDRESS);
      #endif   
    }
  #endif  

  read_DIP();                                     // čteme nastavení DIP spínačů
    
  #ifdef USE_AD
    getBATT();
    if(volt<MIN_BATT) {
      #ifdef DEBUG
         DPRINTLN("Chyba - baterie <5V!");  // pro výpis na UART
      #endif
    }// konec if
    
    while(volt<5.0){ // je malé napětí baterie budeme neustále točit a dál nic nebude dokud bat >5V
       digitalWrite(LED_LOWBAT_PIN,HIGH);   // zapnout LED
       delay(50);
       digitalWrite(LED_LOWBAT_PIN,LOW);    // vypnout LED
       delay(50);
       digitalWrite(LED_LOWBAT_PIN,HIGH);   // zapnout LED
       delay(50);
       digitalWrite(LED_LOWBAT_PIN,LOW);    // vypnout LED
       delay(5000);
       getBATT();
       wdt_reset();                        // vynulovat časovač pro wdt
    }//konec while  
  #endif // AD

  #ifdef USE_DS3231 
    #ifdef DEBUG
       DPRINT("RTC nastavuji interval...");
    #endif
    set_next_alarm();                      // nastavit kdy se probudi CPU podle DIP
    #ifdef DEBUG
       DPRINTLN("OK");
    #endif
  #endif

  #ifdef USE_SERVO
     #ifdef DEBUG
        DPRINTLN("Servo init...");
     #endif

     // OTEVRIT
     pinMode(PWR_SERVO_ON_PIN,OUTPUT);      // napájení serva výstupní pin
     digitalWrite(PWR_SERVO_ON_PIN, HIGH);  // zapnout napájení serva
     servo.attach(SERVO_PIN);               // aktivovat servo
     servo.write(VENTIL_OTEVRENO_UHEL);     // otočit na pozici xx stupňů
     
     #ifdef DEBUG
       DPRINTLN("Oteviram ventil...");
     #endif

     digitalWrite(LED_LOWBAT_PIN,HIGH);     // zapnout LED
     delay(DOBA_PREBEHU_SERVA);             // počkáme než servo dojede
     digitalWrite(LED_LOWBAT_PIN,LOW);      // vypnout LED
     
     digitalWrite(SERVO_PIN,LOW);           // vypnout výstup PWM serva
     digitalWrite(PWR_SERVO_ON_PIN,LOW);    // vypnout napájení serva

     // CEKAT
     for(long t=0; t<ZapNaDobu*60; t++){    // př: 1 minuta = 1000ms * 60 cyklů -> 60 000ms
       digitalWrite(LED_LOWBAT_PIN,HIGH);   // zapnout krátce LED (blik)
       delay(20);                           // 20 + 980 = 1000ms -> 1s
       digitalWrite(LED_LOWBAT_PIN,LOW);    // vypnout LED
       delay(980);
       wdt_reset();                         // vynulovat časovač pro wdt
     }//end for

     // ZAVRIT
     digitalWrite(PWR_SERVO_ON_PIN, HIGH);  // zapnout napájení serva
     servo.attach(SERVO_PIN);               // aktivovat servo
     servo.write(VENTIL_ZAVRENO_UHEL);      // otočit na pozici xx stupňů
     #ifdef DEBUG
       DPRINTLN("Zaviram ventil...");
     #endif

     digitalWrite(LED_LOWBAT_PIN,HIGH);     // zapnout LED
     delay(DOBA_PREBEHU_SERVA);             // počkáme než servo dojede
     digitalWrite(LED_LOWBAT_PIN,LOW);      // vypnout LED

     digitalWrite(SERVO_PIN,LOW);           // vypnout výstup PWM serva
     digitalWrite(PWR_SERVO_ON_PIN,LOW);    // vypnout napájení serva
  #endif  
        
  #ifdef DEBUG
    DPRINT("Vypinam napajeni!");
    delay(1000);
  #endif
  
  digitalWrite(PWR_ON_PIN,LOW);             // vypnout napájení CPU
  while(1);                                 // pokud nespadne CPU sám, tak WDT ho schodí
}//konec setup

void loop(){} // konec loop

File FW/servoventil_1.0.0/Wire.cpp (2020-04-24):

/*
  TwoWire.cpp - TWI/I2C library for Wiring & Arduino
  Copyright (c) 2006 Nicholas Zambetti.  All right reserved.

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
  Modified 2012 by Todd Krein (todd@krein.org) to implement repeated starts
*/
#include <avr/io.h>
#ifdef TWDR
extern "C" {
  #include <stdlib.h>
  #include <string.h>
  #include <inttypes.h>
  #include "twi.h"
}

#include "Wire.h"

// Initialize Class Variables //////////////////////////////////////////////////

uint8_t TwoWire::rxBuffer[BUFFER_LENGTH];
uint8_t TwoWire::rxBufferIndex = 0;
uint8_t TwoWire::rxBufferLength = 0;

uint8_t TwoWire::txAddress = 0;
uint8_t TwoWire::txBuffer[BUFFER_LENGTH];
uint8_t TwoWire::txBufferIndex = 0;
uint8_t TwoWire::txBufferLength = 0;

uint8_t TwoWire::transmitting = 0;
void (*TwoWire::user_onRequest)(void);
void (*TwoWire::user_onReceive)(int);

// Constructors ////////////////////////////////////////////////////////////////

TwoWire::TwoWire()
{
}

// Public Methods //////////////////////////////////////////////////////////////

void TwoWire::begin(void)
{
  rxBufferIndex = 0;
  rxBufferLength = 0;

  txBufferIndex = 0;
  txBufferLength = 0;

  twi_init();
}

void TwoWire::begin(uint8_t address)
{
  twi_setAddress(address);
  twi_attachSlaveTxEvent(onRequestService);
  twi_attachSlaveRxEvent(onReceiveService);
  begin();
}

void TwoWire::begin(int address)
{
  begin((uint8_t)address);
}

void TwoWire::end(void)
{
  twi_disable();
}

void TwoWire::setClock(uint32_t frequency)
{
  TWBR = ((F_CPU / frequency) - 16) / 2;
}

uint8_t TwoWire::requestFrom(uint8_t address, uint8_t quantity, uint32_t iaddress, uint8_t isize, uint8_t sendStop)
{
  if (isize > 0) {
  // send internal address; this mode allows sending a repeated start to access
  // some devices' internal registers. This function is executed by the hardware
  // TWI module on other processors (for example Due's TWI_IADR and TWI_MMR registers)

  beginTransmission(address);

  // the maximum size of internal address is 3 bytes
  if (isize > 3){
    isize = 3;
  }

  // write internal register address - most significant byte first
  while (isize-- > 0)
    write((uint8_t)(iaddress >> (isize*8)));
  endTransmission(false);
  }

  // clamp to buffer length
  if(quantity > BUFFER_LENGTH){
    quantity = BUFFER_LENGTH;
  }
  // perform blocking read into buffer
  uint8_t read = twi_readFrom(address, rxBuffer, quantity, sendStop);
  // set rx buffer iterator vars
  rxBufferIndex = 0;
  rxBufferLength = read;

  return read;
}

uint8_t TwoWire::requestFrom(uint8_t address, uint8_t quantity, uint8_t sendStop) {
  return requestFrom((uint8_t)address, (uint8_t)quantity, (uint32_t)0, (uint8_t)0, (uint8_t)sendStop);
}

uint8_t TwoWire::requestFrom(uint8_t address, uint8_t quantity)
{
  return requestFrom((uint8_t)address, (uint8_t)quantity, (uint8_t)true);
}

uint8_t TwoWire::requestFrom(int address, int quantity)
{
  return requestFrom((uint8_t)address, (uint8_t)quantity, (uint8_t)true);
}

uint8_t TwoWire::requestFrom(int address, int quantity, int sendStop)
{
  return requestFrom((uint8_t)address, (uint8_t)quantity, (uint8_t)sendStop);
}

void TwoWire::beginTransmission(uint8_t address)
{
  // indicate that we are transmitting
  transmitting = 1;
  // set address of targeted slave
  txAddress = address;
  // reset tx buffer iterator vars
  txBufferIndex = 0;
  txBufferLength = 0;
}

void TwoWire::beginTransmission(int address)
{
  beginTransmission((uint8_t)address);
}

//
//  Originally, 'endTransmission' was an f(void) function.
//  It has been modified to take one parameter indicating
//  whether or not a STOP should be performed on the bus.
//  Calling endTransmission(false) allows a sketch to
//  perform a repeated start.
//
//  WARNING: Nothing in the library keeps track of whether
//  the bus tenure has been properly ended with a STOP. It
//  is very possible to leave the bus in a hung state if
//  no call to endTransmission(true) is made. Some I2C
//  devices will behave oddly if they do not see a STOP.
//
uint8_t TwoWire::endTransmission(uint8_t sendStop)
{
  // transmit buffer (blocking)
  int8_t ret = twi_writeTo(txAddress, txBuffer, txBufferLength, 1, sendStop);
  // reset tx buffer iterator vars
  txBufferIndex = 0;
  txBufferLength = 0;
  // indicate that we are done transmitting
  transmitting = 0;
  return ret;
}

//  This provides backwards compatibility with the original
//  definition, and expected behaviour, of endTransmission
//
uint8_t TwoWire::endTransmission(void)
{
  return endTransmission(true);
}

// must be called in:
// slave tx event callback
// or after beginTransmission(address)
size_t TwoWire::write(uint8_t data)
{
  if(transmitting){
  // in master transmitter mode
    // don't bother if buffer is full
    if(txBufferLength >= BUFFER_LENGTH){
      setWriteError();
      return 0;
    }
    // put byte in tx buffer
    txBuffer[txBufferIndex] = data;
    ++txBufferIndex;
    // update amount in buffer
    txBufferLength = txBufferIndex;
  }else{
  // in slave send mode
    // reply to master
    twi_transmit(&data, 1);
  }
  return 1;
}

// must be called in:
// slave tx event callback
// or after beginTransmission(address)
size_t TwoWire::write(const uint8_t *data, size_t quantity)
{
  if(transmitting){
  // in master transmitter mode
    for(size_t i = 0; i < quantity; ++i){
      write(data[i]);
    }
  }else{
  // in slave send mode
    // reply to master
    twi_transmit(data, quantity);
  }
  return quantity;
}

// must be called in:
// slave rx event callback
// or after requestFrom(address, numBytes)
int TwoWire::available(void)
{
  return rxBufferLength - rxBufferIndex;
}

// must be called in:
// slave rx event callback
// or after requestFrom(address, numBytes)
int TwoWire::read(void)
{
  int value = -1;

  // get each successive byte on each call
  if(rxBufferIndex < rxBufferLength){
    value = rxBuffer[rxBufferIndex];
    ++rxBufferIndex;
  }

  return value;
}

// must be called in:
// slave rx event callback
// or after requestFrom(address, numBytes)
int TwoWire::peek(void)
{
  int value = -1;

  if(rxBufferIndex < rxBufferLength){
    value = rxBuffer[rxBufferIndex];
  }

  return value;
}

void TwoWire::flush(void)
{
  // XXX: to be implemented.
}
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

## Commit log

2019-01-10 Založení projektu
    [servoventil.brd, servoventil.sch]
2019-01-12 Rozdělané schéma
    [servoventil.brd, servoventil.sch]
2019-01-14 Schema před kontrolou
    [BOM.csv, servoventil.brd, servoventil.sch]
2019-01-14 Deska spojů, schéma
    vše před kontrolou (až dorazí součástky)
    [servoventil.brd, servoventil.sch]
2019-01-15 Schéma a deska před kontrolou
    [BOM.csv, servoventil.brd, servoventil.sch]
2019-02-04 pcb foto
2019-02-16 oprava chyby na desce
    chyběla zem pod 3,3V stabilizátorem (heatsink + gnd se nespojilo)
    [BOM.csv, servoventil.brd, servoventil.sch]
2019-02-18 Já jsem hotov :-)
    [BOM.csv, servoventil.brd, servoventil.sch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]
2019-02-19 Přidáno schéma
    [BOM.csv, servoventil.brd, servoventil.sch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]
2020-04-26 Create zadig-2.5 (USBasp drivers).exe

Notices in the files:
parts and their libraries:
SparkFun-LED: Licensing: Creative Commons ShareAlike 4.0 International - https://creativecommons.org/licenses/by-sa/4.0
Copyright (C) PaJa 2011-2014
